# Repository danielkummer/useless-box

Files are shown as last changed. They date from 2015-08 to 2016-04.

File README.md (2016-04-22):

# Useless Box
A useless box is basically a machine which turns itself off. However, with a few additional servos, and a little programming, you're able to blow some live into it and give it some "character" - as well as adding a few surprises for the user...

## TL;DR 

A demo video of the box. Because of randomization the video doesn't include _all_ different behavior patterns - there are more...

[Demo Video](https://www.youtube.com/watch?v=xstKcBLtHTI

## Features / Surprises

* Control the door and "hand" separately
* Detect the operator by using a distance sensor
* Wave a white flag
* Hop away
* Ambient light

I've used software debouncing of the switch because it's much easier than including additional wiring and parts.
Although the MotorShield is clearly overkill for this project it reduces the complexity of the required electronics knowledge (and soldering) quite a bit.

## Hardware

### Electronics - Parts List

The following parts were used:

| Amount | Part Type | Properties |
|---|---|---|
| 1 | [Arduino Uno](https://www.arduino.cc/en/Main/arduinoBoardUno) | |
| 1 | [MotorShield](https://www.arduino.cc/en/Main/ArduinoMotorShieldR3) | Rev3 |
| 2 | Basic Servo | You should use a high-torque servo for the arm |
| 1	| Micro Servo | |
| 1	| Infrared Proximity Sensor [Sharp GP2Y0A21YK0F](http://www.sharpsma.com/webfm_send/1489) | 10 - 80 cm |
| 1	| DC Motor | geared |
| 1 | Metallic Toggle Switch | |
| 1 | Plastic Power Switch | |
| 1 | LIPO Battery | 11.1v 1200mAh |
| 1 | Resistor | 10k&#937; Pull-down for switch |
| 2 | [NeoPixel](https://www.adafruit.com/category/168) | |
| 1 | 5V UBEC DC-DC Converter | UBEC 5A Dynam DY-1016-5A |

### Circuit

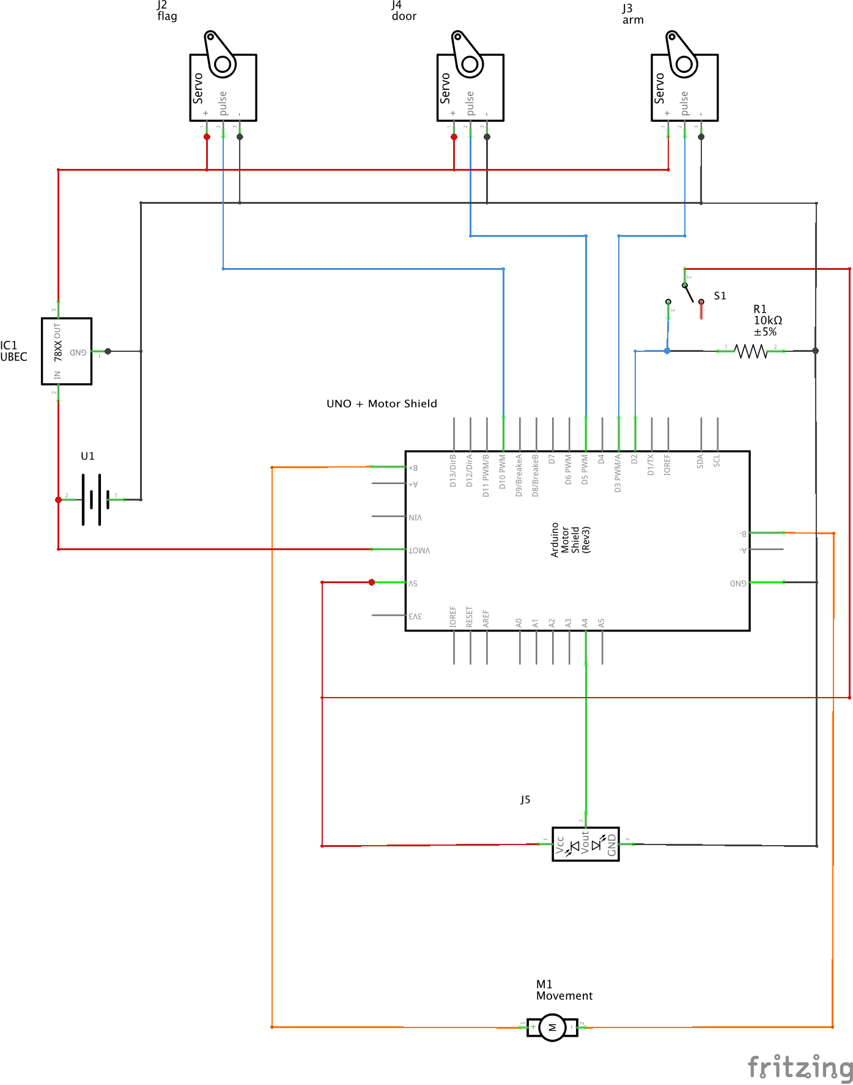
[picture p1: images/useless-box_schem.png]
Circuit Diagram


### Material

* Wooden box with enough space to fit everything into
* Some chipboard ~ 4mm to build the arm and mountings
* Rubber band to force-close the lid
* Hinges
* Cables

### Tools

* Solder
* Jigsaw
* Sanding paper
* Wood glue

## Operation

My useless box fulfills of course the basic functionality of turning itself off.
But using a few additional pieces of equipment it can:

* "Hop" away
* Detect the users distance (and react to it)
* Wave a white flag - but without giving up of course :)

# Software

The box has basically a fixed set of "moves" it can do to turn of the switch after it has been turned on. To make things a little more interesting, the moves are randomly used to surprise the operator.

The whole code is quite easy - there's nothing special about it.
I've created a few bases classes to control every peripheral and another class "Moves" to implement the patterns. This is mainly because the basic Arduino way of programming leads to lots of code duplication and unreadable code.

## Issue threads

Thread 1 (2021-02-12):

Bounce Error?

hpb0002, 2021-02-12:
Hey, I'm new to Arduinos, so I need a bit of help. When I try to upload the code to my Arduino Uno, I get this error:

"Arduino: 1.8.13 (Windows 10), Board: "Arduino Uno"

useless-box:14:10: fatal error: Bounce2.h: No such file or directory

compilation terminated.

exit status 1

Bounce2.h: No such file or directory"

I'm sure I'm missing something, but any help would be appreciated!

barry-ha, 2021-02-13:
hpb0002: Was your question answered?
If not, I will guess you need to install the "Bounce2" library.
In the Arduino workbench, use Tools > Manage Libraries.
Search for Bounce2. Click "Install" and try compiling again.
It resolves the "no such file or directory" message for me. I did get more compile errors but I can't help you there; it's not my project. You might need to get more libraries, for any include that uses angle brackets such as "#include <Servo.h>"
Good luck from a random passerby, Barry

alexandrosk0, 2021-02-13:
Thanks @barry-ha.
I didn't document the arduino IDE setup, but this project is really nothing extra besides valina arduino code with servos and serial logging.

If there anything I can help, just let me know.

barry-ha, 2021-02-13:
Hi Alex, I know it's been several years, but can you update README.md to suggest a part for the micro servo and higher torque servo? I want to build my own useless box; I'm good with Arduino but don't know where to start choosing servos. The choices on Amazon are overwhelming.
Many thanks, Barry

Closed 2021-02-12.

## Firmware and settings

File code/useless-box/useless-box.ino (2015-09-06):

//#define ENABLE_PRINT

#ifdef ENABLE_PRINT
  #define Sprintln(a) (Serial.println(a))
  #define Sprint(a) (Serial.print(a))
  #define Sbegin(a) (Serial.begin(a))
#else   
  #define Sprintln(a)
  #define Sprint(a)
  #define Sbegin(a)
#endif

#include <Servo.h>
#include <Bounce2.h>
#include <Adafruit_NeoPixel.h>

#include "MotorControl.h"
#include "ServoControl.h"

/*
 * Servo positions
 */ 
#define MIN_ARM_DEG 35
#define MAX_ARM_DEG 165
#define POS_ARM_HOME MIN_ARM_DEG
#define POS_SWITCH_ARM MAX_ARM_DEG
#define POS_ARM_PEEK (MIN_ARM_DEG + 70)
#define POS_ARM_CHECK_NINJA (MIN_ARM_DEG + 20) 
#define POS_ARM_NEAR_SWITCH (MAX_ARM_DEG - 50)
//-------------------------------------------------
#define MIN_DOOR_DEG 95
#define MAX_DOOR_DEG 40
#define POS_DOOR_HOME MIN_DOOR_DEG
#define POS_DOOR_MEDIUM_OPEN (POS_DOOR_HOME - 32) 
#define POS_DOOR_FULL_OPEN MAX_DOOR_DEG
#define POS_DOOR_CHECK_NINJA (POS_DOOR_HOME - 20)
#define POS_DOOR_FLAP POS_DOOR_HOME - 20
//-------------------------------------------------
#define MIN_FLAG_DEG 55
#define MAX_FLAG_DEG 160
#define POS_FLAG_HIDDEN MIN_FLAG_DEG
#define POS_FLAG_RAISED MAX_FLAG_DEG
#define POS_FLAG_TILTED (MAX_FLAG_DEG - 40)
//-------------------------------------------------
// 
#define MECANIC_SPEED_PER_DEGREE 2  // the number of msec (approx.) for the servo to go one degree further
#define MECANIC_DELAY_SWITCH 70     // the delay between the arm hitting the switcha and the switch reporting a change in value 
//-------------------------------------------------
#define IMPATIENT_INTERVAL_THRESHOLD 7  //times the interval must be triggered before impatient mode is activated
#define IMPATIENT_INTERVAL_TIME 20000
#define IMPATIENT_MODE_TIMEOUT 30000
#define NUM_MAX_IMPATIENT_ACTION 7      //number of impatient actions - while the box stays in impatient mode


#define NUM_BEHAVIOURS 19

/*
 * I/O
 */ 
#define ARM_SERVO_PIN   9
#define DOOR_SERVO_PIN  6
#define FLAG_SERVO_PIN  5
#define DIRECTION_PIN   13
#define THROTTLE_PIN    11
#define DISTANCE_PIN    A4
#define BOX_SWITCH_PIN  2
#define PIXEL_PIN       10

/*
 * Operation
 */ 
Bounce bouncer = Bounce();
int activated = LOW;

int selectedBehaviour = 1;        // This is used to choose the next behaviour 
long randCheck = 1;               // Random check when not activated
boolean hasAlreadyChecked = true; // Set when box has checked the switch (peeked at it)
boolean interrupted = false;      // Is set to true when the switch has been changed while doing something. Allows for a quick check in the loop() for what we should do next

//Distance detection
int lastDistance = 0;             // Last measured distance
int threshold = 200;              // Distance threshold
unsigned long timer;              // Distance timer

// Impatient mode variables
int impatientCount = 0;           // How many impatient actions were done
int impatientThresholdCount = 0;  // How may times was the switch operated in short intervals
boolean impatient = false;        // is the box impatient
unsigned long activatedTimestamp; // When fwas the box last activated

MotorControl motor = MotorControl();
ServoControl arm = ServoControl("arm");
ServoControl door = ServoControl("door");
ServoControl flag = ServoControl("flag");
Adafruit_NeoPixel pixels = Adafruit_NeoPixel(2, PIXEL_PIN, NEO_GRB + NEO_KHZ800);

/*
 * Colors
 */ 
uint32_t black = pixels.Color(0, 0, 0);
uint32_t red =  pixels.Color(255, 0, 0);
uint32_t yellow = pixels.Color(255, 194, 0);
uint32_t orange = pixels.Color(255,146,0);
uint32_t orangeRed = pixels.Color(255,65,0);
uint32_t blue = pixels.Color(11,97,164);
uint32_t impatientColors[] = {
  pixels.Color(255, 194, 0), //yellow
  pixels.Color(255,146,0),   //orange
  pixels.Color(255,65,0),    //orangeRed
  pixels.Color(234,0,55),    //purplered
  pixels.Color(255, 0, 0),   //red
  pixels.Color(255, 0, 0),   //red
  pixels.Color(255, 0, 0),   //red
  pixels.Color(11,97,164)    //blue  
};

/*
 * Setup
 */ 
void setup() {  
  pinMode(BOX_SWITCH_PIN, INPUT);
  pinMode(DIRECTION_PIN, OUTPUT);  
  pinMode(DISTANCE_PIN,INPUT);
  
  Sbegin(9600);
  Sprintln(F("Started.")); 
  Sprintln(F("Initializing positions."));

  bouncer.attach(BOX_SWITCH_PIN);
  motor.attach(DIRECTION_PIN, THROTTLE_PIN);
  arm.attach(&bouncer, ARM_SERVO_PIN, POS_ARM_HOME, POS_SWITCH_ARM);
  door.attach(&bouncer, DOOR_SERVO_PIN, POS_DOOR_HOME, POS_DOOR_FULL_OPEN);
  flag.attach(&bouncer, FLAG_SERVO_PIN, POS_FLAG_HIDDEN, POS_FLAG_RAISED);
  
  activatedTimestamp = IMPATIENT_INTERVAL_TIME + 1;

  //initializeneopixels
  pixels.begin();
  pixels.show();
  pixels.setBrightness(255); 
  randomSeed(analogRead(0));      
}

/**
 * A "soft" delay function - This function can be interrupted by manual switch change.
 * If interrupted the method returns early and sets the interruped state variable to true.
 * The soft delay function returns the value of the switch
 */
int softDelay(int msec) {
  Sprint(F("Delaying for "));
  Sprint(msec);
  Sprintln(F(" msec...")); 
  bouncer.update();
  int val = bouncer.read();
  int current_value;
  long time_counter = 0;  
  do {
    delay(1);
    time_counter++;
    bouncer.update();
    current_value = bouncer.read();
    if (current_value != val) {
      Sprintln(F("/!\\[Soft Delay] Interrupted - The switch was operated while I was waiting on purpose !"));
      interrupted = true;
      break;
    }
  } while(time_counter <= msec);
  return current_value;
}

/**
 * Detect movement inside a given threshold
 */
boolean detect(int detectionTime) {
  int currentDistance;
  delay(1200);    //wait to stabilize sensor readings after opening the door   
  timer = millis();
  //interrupt if bouncer value changes
  // wait for movement that exceeds threshold or if timer expires (5 sec),
  bouncer.update();
  int oldButtonValue = bouncer.read();
  
  while(millis() - timer <= detectionTime - 1200) {
    currentDistance = analogRead(DISTANCE_PIN);        
    Sprint(F("Current Distance"));
    Sprintln(currentDistance);
    if(currentDistance >= 380) { // The users hand is near the switch!
      Sprintln(F("Detected!"));
      return true;
    }    
    delay(500);

    //exit loop if switch is on
    /*bouncer.update();
    int newButtonValue = bouncer.read();
    if(oldButtonValue != newButtonValue && newButtonValue == HIGH) {
      break;
    }*/    
  }
  return false;
}

/**
 * Reset operation to normal mode, reposition arm and door
 */
void resetToNormalMode() {
  Sprintln(F("Getting tired, leaving impatient mode..."));      
  impatientCount = 0;
  impatient = false;
  arm.reattach();
  door.reattach();    
  door.setHome(POS_DOOR_HOME);
  door.isHome(false);  
  arm.setHome(POS_ARM_HOME);    
  arm.isHome(false);  
}

/**
 * Set operation mode to impation mode, reposition arm and door
 */
void setImpatientMode() {
  Sprintln(F("Alright, thats it! I'm getting impatient!"));
  impatient = true;    
  impatientThresholdCount = 0;     
  arm.isHome(false);
  arm.setHome(POS_ARM_PEEK);      
  door.isHome(false);
  door.setHome(POS_DOOR_MEDIUM_OPEN);            
  delay(100);
}

/**
 * Get the next normal behaviour
 */
int determineNormalBehaviour() {            
  int newBehaviour;
  do {
    newBehaviour = random(1, NUM_BEHAVIOURS);      
  } while (newBehaviour == selectedBehaviour );
  selectedBehaviour = newBehaviour;    
  return newBehaviour;  
}

/**
 * Get the next behaviour for impatient mode
 */
int determineImpatientBehaviour() {     
  int result = 1;
  //define "special" moves
  switch(impatientCount) {
    case NUM_MAX_IMPATIENT_ACTION - 3:
      result = 9; break;
    case NUM_MAX_IMPATIENT_ACTION - 2:
      result = 101; break;
    case NUM_MAX_IMPATIENT_ACTION - 1: 
      result = 100; break;
    case NUM_MAX_IMPATIENT_ACTION:
      result = 102; break;
    default:
      break;
  }  
  return result;
}

void setRgbColor(byte red, byte green, byte blue) {
  setColor(pixels.Color(red, green, blue));
}

void setColor(uint32_t color) {
  pixels.setPixelColor(0, color); 
  pixels.setPixelColor(1, color); 
  pixels.show();
}

void pulseColor(uint32_t color, byte times) {
  for(byte i = 0; i < times; i++) {
    setColor(color);
    delay(100);
    setColor(black);
    delay(100);
  }
}

// Input a value 0 to 255 to get a color value.
// The colours are a transition r - g - b - back to r.
uint32_t wheel(byte wheelpos) {
  wheelpos = 255 - wheelpos;
  if(wheelpos < 85) {
    return pixels.Color(255 - wheelpos * 3, 0, wheelpos * 3);
  }
  if(wheelpos < 170) {
    wheelpos -= 85;
    return pixels.Color(0, wheelpos * 3, 255 - wheelpos * 3);
  }
  wheelpos -= 170;
  return pixels.Color(wheelpos * 3, 255 - wheelpos * 3, 0);
}

/* ------------------------------- */
/* ---- STANDARD BEHAVIOURS ------ */
/* ------------------------------- */

void flipSwitch(int msec = 0) { 
  interrupted = arm.move(POS_SWITCH_ARM, msec); 
  delay(MECANIC_DELAY_SWITCH); // Wait for the switch to acknowledge before returning in the loop
}

// Go near the arm, but not as close as to push the switch, and then retracts a bit
void tryFail(int msec = 0) {  
  interrupted = arm.move(POS_ARM_NEAR_SWITCH, msec);
  interrupted = arm.move(POS_ARM_NEAR_SWITCH + 7, msec); 
}

// Open the lid stealthly. User does not see me. I'm a NINJA !
void goStealthCheck() {    
  interrupted = arm.move(POS_ARM_CHECK_NINJA, 30);
  interrupted = arm.move(POS_ARM_NEAR_SWITCH + 7, 30);  
}

void openDoorNinja(int msec = 0) {
  interrupted = door.move(POS_DOOR_CHECK_NINJA, msec);
}

void openDoorFlap(int msec = 0) {
  interrupted = door.move(POS_DOOR_FLAP, msec);  
}

void openDoorMedium(int msec = 0) {
  interrupted = door.move(POS_DOOR_MEDIUM_OPEN, msec);  
}

void openDoorFull(int msec = 0) {
  interrupted = door.move(POS_DOOR_FULL_OPEN, msec);
}

// Ok, back home now
void backHome() { 
  int homePosArm = impatient ? POS_ARM_PEEK : POS_ARM_HOME;
  arm.move(homePosArm, 0); 
}

// Open the lid to see out
void goCheck(int msec = 0) {  
  interrupted = arm.move(POS_ARM_PEEK, msec); 
}

void closeDoor(int msec = 0) {
  int homePos = impatient ? POS_DOOR_MEDIUM_OPEN : POS_DOOR_HOME;  
  interrupted = door.move(homePos, msec);
}


void raiseflag(int msec = 0) {
  interrupted = flag.move(POS_FLAG_RAISED, msec);
}

void tiltflag(int msec = 0) {
  interrupted = flag.move(POS_FLAG_TILTED, msec);
}

void hideflag(int msec = 0) {
  interrupted = flag.move(POS_FLAG_HIDDEN, msec);  
}

void waveflag(int times) {
  byte i;
  raiseflag();  
  delay(100);
  for (i = 0; i < times; i++) {    
    tiltflag();
    delay(15);    
    //door.move(POS_DOOR_FULL_OPEN, 0); //damn this hack
    raiseflag();    
  }  
  delay(70);
  hideflag();  
}

/* ------------------------------------ */
/* ---- INTERRUPTABLE BEHAVIOURS ------ */
/* use these for the concrete movements */
/* ------------------------------------ */

// Go out and flip that switch the user just
void goOpenDoorAndFlipThatSwitch(int msec = 0) { 
  if (!interrupted) openDoorMedium(msec);
  if (!interrupted) flipSwitch(msec);
}

void driveAway(){
  if (!interrupted) openDoorMedium();
  if (!interrupted) motor.forward(100);
  if (!interrupted) softDelay(2000);  
  if(!interrupted && detect(3000)) {
    Sprintln(F("Detected movement!"));
    if (!interrupted) motor.backward(100);
    if (!interrupted) softDelay(800);
    if (!interrupted) motor.halt();
  }
  motor.halt();
  if (!interrupted) goOpenDoorAndFlipThatSwitch();  
}

void whiteflag() 
{  
  flag.isHome(false);  
  openDoorFull();
  waveflag(7);
  flag.isHome(true);  
  softDelay(500);  
  if (!interrupted) flipSwitch();   
}

// Check once, wait, then flip the switch
void check() {
  if (!interrupted) openDoorMedium();
  if (!interrupted) goCheck(random(0, 10));
  if (!interrupted) softDelay(1000);
  if (!interrupted) goOpenDoorAndFlipThatSwitch();
}

// Check, return back home, then flip
void checkReturn() {
  if (!interrupted) openDoorMedium();
  if (!interrupted) goCheck(random(0,10));
  if (!interrupted) softDelay(1500);
  if (!interrupted) backHome();
  if (!interrupted) softDelay(600);
  if (!interrupted) goOpenDoorAndFlipThatSwitch();
}

// Multi tries. At the end, succeeds...
void multiTry() {
  if (!interrupted) openDoorMedium();
  if (!interrupted) tryFail(5);
  if (!interrupted) softDelay(500);
  if (!interrupted) tryFail(5);
  if (!interrupted) softDelay(500);  
  if (!interrupted) backHome();
  if (!interrupted) softDelay(200);
  if (!interrupted) goOpenDoorAndFlipThatSwitch();
}

// Check once slowly, return, check again, return to stealth position, then flip
void checkCheckReturn() { //not ok
  if (!interrupted) openDoorNinja(30);
  if (!interrupted) openDoorMedium();
  if (!interrupted) goStealthCheck();
  if (!interrupted) softDelay(1000);
  if (!interrupted) backHome();
  if (!interrupted) closeDoor();
  if (!interrupted) openDoorMedium();
  if (!interrupted) goCheck(10);
  if (!interrupted) backHome();
  if (!interrupted) closeDoor();
  if (!interrupted) softDelay(700);
  if (!interrupted) openDoorNinja(30);
  if (!interrupted) goStealthCheck();
  if (!interrupted) softDelay(500);
  if (!interrupted) goOpenDoorAndFlipThatSwitch();
}

void afraid() {
  if (!interrupted) openDoorMedium();
  if (!interrupted) tryFail();  
  if (!interrupted) goCheck();
  if (!interrupted) backHome();
  if (!interrupted) closeDoor();
  if (!interrupted) softDelay(1000);
  if (!interrupted) openDoorMedium(20);
  if (!interrupted) flipSwitch(15);
}

// #OhWait 
void ohWait() {
  if (!interrupted) openDoorMedium();
  if (!interrupted) tryFail();
  if (!interrupted) backHome();
  if (!interrupted) openDoorMedium();
  if (!interrupted) softDelay(700);
  if (!interrupted) goCheck(2); // Woops. Forgot something ?
  if (!interrupted) softDelay(1000);
  if (!interrupted) goOpenDoorAndFlipThatSwitch(random(0,15));
}

void matrix() {
  if (!interrupted) openDoorMedium();
  if (!interrupted) goCheck(10);  
  if (!interrupted) flipSwitch(30);
  if (!interrupted) softDelay(300);  
}

void crazyDoor() {
  if (!interrupted) openDoorMedium(random(7,15));
  if (!interrupted) closeDoor();
  if (!interrupted) softDelay(700);
  if (!interrupted) openDoorFull(random(0,10));    
  if (!interrupted) softDelay(500);  
  if (!interrupted) closeDoor();  
  if (!interrupted) openDoorFull(random(0,20));      
  if (!interrupted) flipSwitch(random(5,20));  
}

void crazySlow() { //ok  
  if (!interrupted) goOpenDoorAndFlipThatSwitch(30);  
}

void flappingAround() {
  int i;
  for(i = 0; i < 5; i++) {
    if (!interrupted) openDoorFull(10);
    if (!interrupted) closeDoor();    
    if (!interrupted) softDelay(200);         
  }
  if (!interrupted) goOpenDoorAndFlipThatSwitch();   
}

void lowFlappingAround() {
  int i;
  for(i = 0; i < 5; i++) {
    if (!interrupted) openDoorFlap(0);
    if (!interrupted) closeDoor();        
  }  
  if (!interrupted) softDelay(300);         
  if (!interrupted) goOpenDoorAndFlipThatSwitch();   
}

void vibrating() {
  if (!interrupted) openDoorMedium();
  if (!interrupted) tryFail();  
  if (!interrupted) tryFail();
  if (!interrupted) tryFail();
  if (!interrupted) tryFail();
  if (!interrupted) tryFail();
  if (!interrupted) tryFail();
  if (!interrupted) tryFail();
  if (!interrupted) backHome();
  if (!interrupted) goOpenDoorAndFlipThatSwitch();  
}

void moveBackAndForth() {  
  if (!interrupted) motor.forward(100);
  if (!interrupted) softDelay(600); 
  if (!interrupted) motor.backward(100);
  if (!interrupted) softDelay(600); 
  if (!interrupted) motor.forward(100);  
  if (!interrupted) softDelay(600); 
  if (!interrupted) motor.backward(100);
  if (!interrupted) softDelay(700); 
  if(!interrupted && detect(3000)) {
    Sprintln(F("Detected movement!"));
    if (!interrupted) motor.forward(100);
    if (!interrupted) softDelay(300);
    if (!interrupted) motor.halt();
  }  
  motor.halt();
  if (!interrupted) openDoorNinja(30);  
  if (!interrupted) goOpenDoorAndFlipThatSwitch();  
}

void turnOffThenWait() {  
  arm.interruptable(false);
  if (!interrupted) goOpenDoorAndFlipThatSwitch(0);
  if (!interrupted) goCheck();
  arm.interruptable(true);
  if (!interrupted) softDelay(2000);  
}

void turnOffwaitAndFlipDoor() {
  arm.interruptable(false);
  if (!interrupted) goOpenDoorAndFlipThatSwitch(0);  
  int i;
  for(i = 0; i < 3; i++) {
    if (!interrupted) openDoorFull(0);    
    if (!interrupted) openDoorMedium(5);      
  }  
  arm.interruptable(true);  
  if (!interrupted) softDelay(500);    
}

void angryTurnOff() {
  arm.interruptable(false);
  goOpenDoorAndFlipThatSwitch();  
  backHome();
  goOpenDoorAndFlipThatSwitch();  
  backHome();
  goOpenDoorAndFlipThatSwitch();
  arm.move(POS_ARM_HOME, 0);
  arm.interruptable(true);
  if (!interrupted) softDelay(300);  
  door.move(POS_DOOR_FULL_OPEN, 0);  
  flag.isHome(false);  
  //openDoorFull();
  waveflag(7);  
  hideflag();  
  flag.isHome(true);  
  //arm.move(POS_ARM_HOME, 0);   
  //door.move(POS_DOOR_HOME, 0);
  pulseColor(red, 3);
}

/**
 * TODO when user is detected
 * 1. drive away
 * 2. flap door
 * 3. ??
 * 
 */
//working debug test
void turnOffIfUserIsDetected() {
  int i;
    for (i = 0; i < random(3, 5); i++) {
    openDoorMedium(15);
    flipSwitch();
    backHome();   
    //TODO should turn off immediatly if turned on during detection 
    if (detect(10000)) {        
      bouncer.update();
      if(bouncer.read() == HIGH) { 
        flipSwitch();
        backHome();   
      } else {
        goCheck(random(0, 15));                         
      }      
    }
    if(softDelay(5000) == LOW) {
        break;    
    }
  }  
}

void randomCheck() {
  hasAlreadyChecked = true;
  arm.isHome(false);         
  if (!interrupted) arm.reattach();
  if (!interrupted) door.reattach();            
  if (!interrupted) goCheck(5);
  if (!interrupted) softDelay(1000);      
}

/*
 * Loop
 */ 
void loop() {  
  bouncer.update();
  activated = bouncer.read();

  //reset to normal mode after NUM_MAX_IMPATIENT_ACTION actions have been performed;
  if(impatient && impatientCount >= NUM_MAX_IMPATIENT_ACTION) {       
    resetToNormalMode(); 
  }  

  // set to impatient mode if conditions are met
  if (!impatient && impatientThresholdCount >= IMPATIENT_INTERVAL_THRESHOLD ) {
    setImpatientMode();
    //TODO: Debug led, remove      
  }  
  
  /*if (flag.isHome() == false) {    
    Sprintln(F("Hiding flag"));
    hideflag();        
  } else*/
  if (arm.isHome() == false) {    
    Sprintln(F("Going back home"));
    backHome();        
  } else if (door.isHome() == false) {
    Sprintln(F("Closing door"));
    closeDoor();     
  } else if (randCheck < 5 && hasAlreadyChecked == false) {                
    Sprintln(F("Random check, baby. "));            
    randomCheck();
  }  else if (activated == HIGH) {    
    Sprintln(F("Who turned me on?"));
    
    arm.isHome(false);
    door.isHome(false);
    
    arm.reattach();
    door.reattach();
    flag.reattach();
       
    if(impatient) {
      Sprint(F("I'm impatient right now - for the "));       
      impatientCount++;
      Sprint(impatientCount);
      Sprintln(F(" time!"));
    } else if (!impatient && (millis() - activatedTimestamp <= IMPATIENT_INTERVAL_TIME)) { 
      //increase impatient trigger count if box is operated repeatedly in interval   
      impatientThresholdCount++;
      Sprint(F("Getting impatient... "));
      Sprint(impatientThresholdCount);
      Sprint(F(" of "));
      Sprintln(IMPATIENT_INTERVAL_THRESHOLD);
      Sprint(F("Time difference is: "));
      Sprintln(millis() - activatedTimestamp);      
    }      

    //use specific moves in impatient mode and set the correct color
    if (impatient) {
      selectedBehaviour = determineImpatientBehaviour(); 
      setColor(impatientColors[impatientCount % NUM_MAX_IMPATIENT_ACTION]); 
    } else {      
      selectedBehaviour  = determineNormalBehaviour();
      setColor(wheel(random(0,255)));       
    } 

    //update activated after impatient check
    activatedTimestamp = millis();

    Sprint(F("-------- Starting behaviour: ["));
    Sprint(selectedBehaviour);
    Sprintln(F("]"));
    Sprint(F("-------- "));
    switch(selectedBehaviour) { 
      case 1: Sprintln(F("Normal flip")); goOpenDoorAndFlipThatSwitch(); break;
      case 2: Sprintln(F("Check")); check(); break;
      case 3: Sprintln(F("Multi try")); multiTry(); break;
      case 4: Sprintln(F("Check and return")); checkReturn(); break;
      case 5: Sprintln(F("Check, check and return")); checkCheckReturn(); break;
      case 6: Sprintln(F("Afraid")); afraid(); break;
      case 7: Sprintln(F("Oh, wait")); ohWait(); break;
      case 8: Sprintln(F("Crazy slow")); crazySlow(); break;        
      case 9: Sprintln(F("Matrix")); matrix(); break;
      case 10: Sprintln(F("Crazy door")); crazyDoor(); break;
      case 11: Sprintln(F("Drive away")); driveAway(); break;      
      case 12: Sprintln(F("Back and Forth")); moveBackAndForth(); break;
      case 14: Sprintln(F("low flapping around")); lowFlappingAround(); break;  
      case 15: Sprintln(F("turn off, wait")); turnOffThenWait(); break;  
      case 16: Sprintln(F("long wait after turnoff")); turnOffwaitAndFlipDoor(); break; 
      //case 17:  Sprintln(F("White flag")); whiteflag(); break;         
      case 18: Sprintln(F("Measure Distance")); turnOffIfUserIsDetected(); break;    
      case 100: Sprintln(F("Vibrating")); vibrating(); break;  
      case 101: Sprintln(F("Flapping door around")); flappingAround(); break;      
      case 102: Sprintln(F("Angry turn-off")); angryTurnOff(); break;
      default: Sprintln(F("Default")); goOpenDoorAndFlipThatSwitch(); break;   
      }       
      interrupted = false; //reset the interrupted state - i'm done now...
  } // end switch-if   

  //turn off leds after 20sec inactivity
  if (millis() - activatedTimestamp >= 20000 ) {
    setColor(black);
  }
  
  arm.waitAndDetatch();
  door.waitAndDetatch();
  flag.waitAndDetatch();  
  randCheck = random(1, 500000);  
}

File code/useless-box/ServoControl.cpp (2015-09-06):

#if defined(ARDUINO) && ARDUINO >= 100
#include "Arduino.h"
#else
#include "WProgram.h"
#endif
#include "ServoControl.h"

#if defined(ENABLE_PRINT)
  #define Sprintln(a) (Serial.println(a))
  #define Sprint(a) (Serial.print(a))
#else   
  #define Sprintln(a)
  #define Sprint(a)
#endif

#define MECANIC_SPEED_PER_DEGREE 5 // 2 msec to move 1 degree #define MECANIC_SPEED_PER_DEGREE 2 // 2 msec to move 1 degree

ServoControl::ServoControl(char name[]) {
  this->name = name;
  this->current_speed = 0;
  this->pos_home = 15; //set the home position to 15 deg, just an arbitary value, must be set in the attack method
  this->servo = Servo();
  this->is_interruptable = true;
}

void ServoControl::attach(Bounce* bouncer, int pin, int pos_home, int pos_max) {
  this->pin = pin;
  this->pos_home = pos_home;
  this->pos_max = pos_max;
  this->bouncer = bouncer;
  this->servo.write(pos_home);
  this->servo.attach(pin);
}

void ServoControl::interruptable(bool interruptable) {
  this->is_interruptable = interruptable;
}

bool ServoControl::move(int degree, int speed) {
  this->current_speed = speed;
  return move(degree);
}

bool ServoControl::move(int degree) {

  bool interrupted = false;

  Sprint(F("Moving "));
  Sprint(F(this->name));
  Sprint(F(" to position : "));
  Sprint(F(degree));
  Sprintln(F("deg."));

  bouncer->update();
  int switch_value_before_move = bouncer->read();

  // Check the last command we gave to the servo
  int current_degree = servo.read();
  last_write = current_degree;


  // And then moves ! degree by degree, checking the switch position each time
  //while (current_degree != degree) {
  while (current_degree != degree) {
    if (current_degree < degree) {
      current_degree++;
    } else {
      current_degree--;      
    }
    servo.write(current_degree);
    delay(MECANIC_SPEED_PER_DEGREE + this->current_speed);

    // Read switch again in loop so we can react if something changes
    bouncer->update();
    int current_value = bouncer->read();
    if (this->is_interruptable && current_value != switch_value_before_move) {
      //a bit unlucky but i can't really rely on the arm switch of position, so I'm going for a "soft" trigger here
      //Todo this check is really crappy - there must be a better way...
      if (strcmp(this->name, "arm") != 0 ) {              
        if (this->pos_max > this->pos_home) {
            //condition is inverted, only interrupt if not true
           if (current_degree <= this->pos_max - 5 || current_degree >= this->pos_home + 5) {
            interrupted = true;   
           }         
        } else {
           if (current_degree >= this->pos_max - 5 || current_degree <= this->pos_home + 5) {
            interrupted = true;
           }
        } 
      }

         if(interrupted) {
          Serial.print(this->name);
          Serial.print(F(" : "));
          Serial.println(F("/!\\ Interrupted - The switch was operated while I was moving !"));  
        }                
        break;
    }          
  }
  return interrupted;
}

uint8_t ServoControl::getLastWrite() {
  return this->last_write;
}

void ServoControl::waitAndDetatch() {
  if (this->servo.read() == pos_home && this->is_home == false) {
    Sprint(F("Powering off the "));
    Sprint(this->name);
    Sprintln(F(" servo ..."));
    int time_to_wait = abs(this->last_write - pos_home) * (this->current_speed + MECANIC_SPEED_PER_DEGREE);
    delay(time_to_wait);
    this->is_home = true;
    servo.detach();
  }
}

bool ServoControl::isHome() {
  return this->is_home;  
}

void ServoControl::isHome(bool home) {
  this->is_home = home;
}

void ServoControl::setHome(int pos_home) {  
  this->pos_home = pos_home;
}

void ServoControl::reattach() {
  servo.attach(pin);
}

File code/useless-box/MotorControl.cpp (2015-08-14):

#if defined(ARDUINO) && ARDUINO >= 100
#include "Arduino.h"
#else
#include "WProgram.h"
#endif
#include "MotorControl.h" 

MotorControl::MotorControl() {}

void MotorControl::forward(int speed){
  digitalWrite(directionPin, HIGH); //Establishes LEFT direction of Channel B  
  analogWrite(throttlePin, speed);   //Spins the motor on Channel B at half speed
}

void MotorControl::attach(int directionPin, int throttlePin) {
  this->directionPin = directionPin;
  this->throttlePin = throttlePin;
  pinMode(directionPin, OUTPUT);  
}

void MotorControl::backward(int speed)
{
  digitalWrite(directionPin, LOW); //Establishes LEFT direction of Channel B  
  analogWrite(throttlePin, speed);   //Spins the motor on Channel B at half speed
}

void MotorControl::halt()
{
  analogWrite(throttlePin, 0);   //Spins the motor on Channel B at half speed
}

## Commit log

2015-08-14 Change arm pin
2015-08-15 Adjust servos
2015-08-16 Don't react to interrupt on arm servo
2015-08-25 Update code (broke flag)
    [ServoControl.cpp, useless-box.ino]
2015-08-31 Move code to subfolder, add fritzing schema
    [useless-box.fzz]
2015-09-04 refactor code, add leds
    [useless-box.fzz]
2015-09-06 Update code, schema
    [useless-box.fzz]
